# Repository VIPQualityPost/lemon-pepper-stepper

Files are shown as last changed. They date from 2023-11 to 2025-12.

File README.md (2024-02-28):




# Lemon Pepper Stepper Driver
Small, all in one hybrid stepper + BLDC driver, designed to mount to the back of NEMA 14/17 size stepper motors. The board supports up to 48V @ 1.5A with a choice of either step-dir, CAN bus, I2C, UART or USB input. Additionally, there are 5 GPIO broken out that can be used for a second encoder (AB hardware encoder or I2C), endstops or other general purposes. Current sensing is also included on-board.
The boards can easily be assembled by JLC and the design has been cost-optimized, coming in at about $20 per board fully assembled (minus connectors, which need to be modified to sit flat on motor back). 

Due to the high pole pair count of stepper motors, a high resolution (21 bit) magnetic encoder is used, supporting both SPI and hardware ABI position encoding. 
Despite the rather high theoretical performance of this board I think you would need some serious cooling to actually hit the potential 50-70W specs of the parts. A heatsink has been designed and produced that works well with the board, giving a uniform back profile and small fins for heat dissipation.
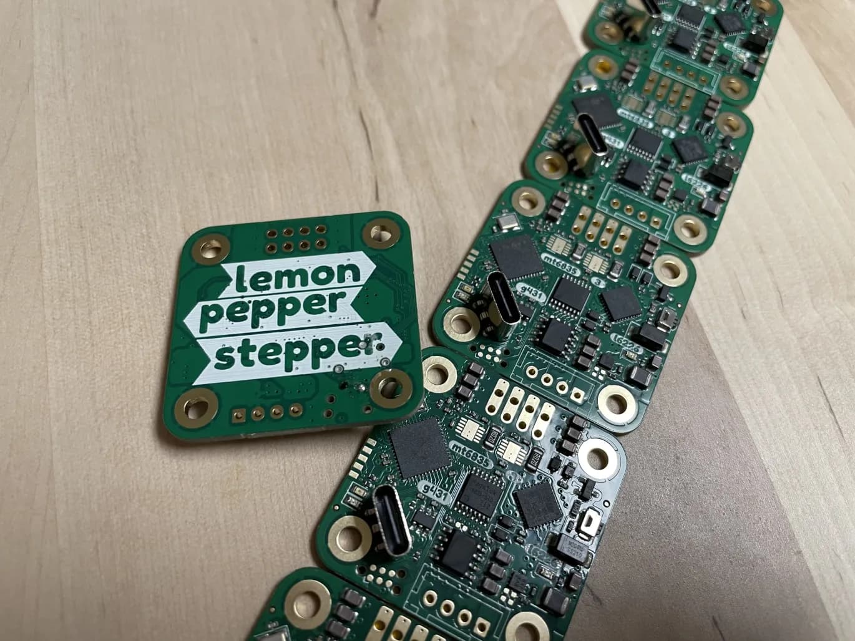
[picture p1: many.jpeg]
Photo of PCB

PCB on motor
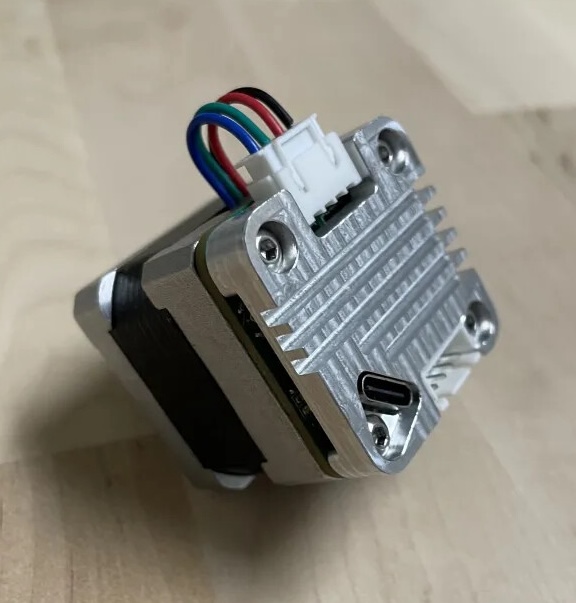
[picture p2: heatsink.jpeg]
Heatsink on motor


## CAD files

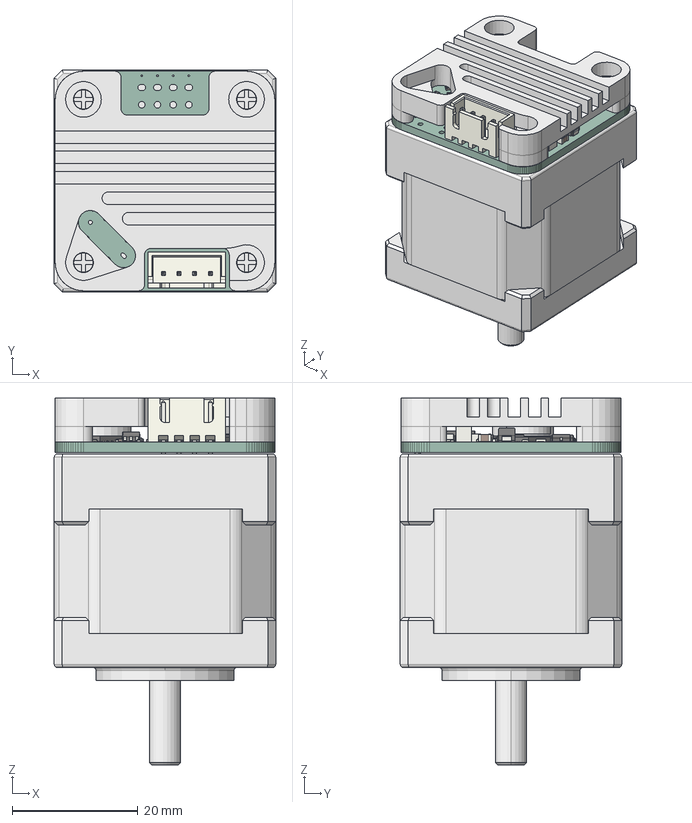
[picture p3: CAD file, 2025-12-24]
mechanical/pcb2blender/lps-assembly.step
35.3 x 35.3 x 58.5 mm
lemon-pepper PCB
6627T38_Stepper Motor

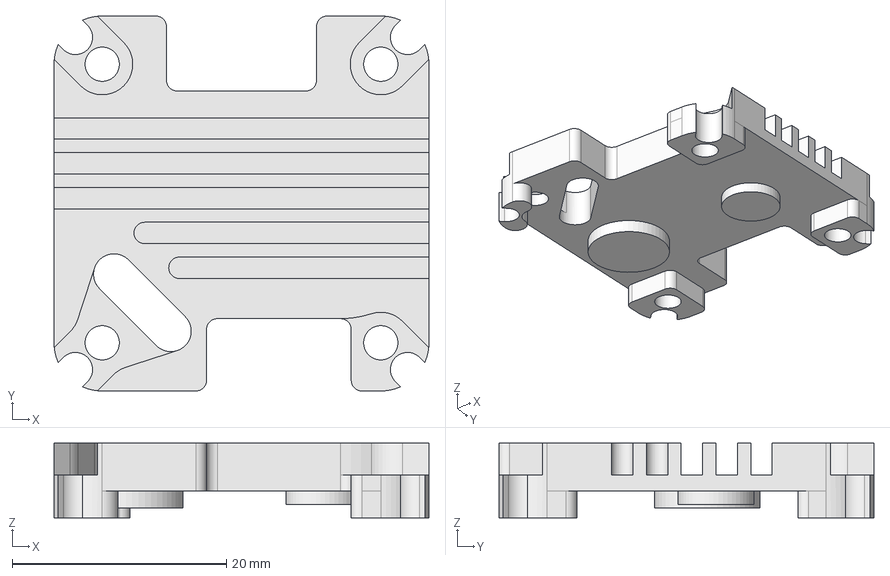
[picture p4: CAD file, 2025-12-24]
mechanical/heatsink-nema-14-17.step
35.0 x 35.0 x 7.00 mm

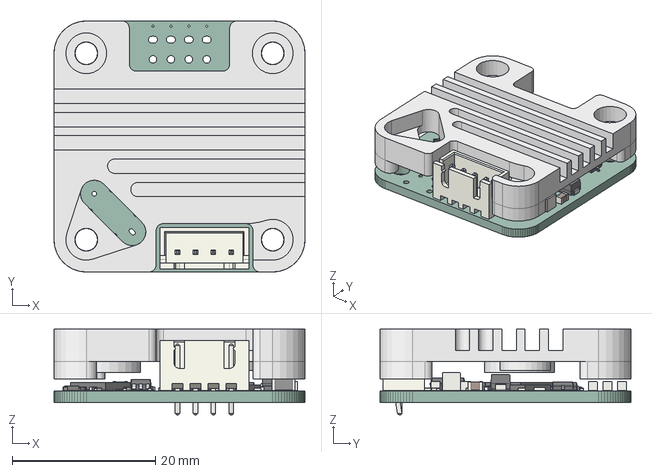
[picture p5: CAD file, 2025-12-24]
mechanical/pcb2blender/lemon-pepper.step
35.0 x 35.0 x 12.0 mm
lemon-pepper PCB

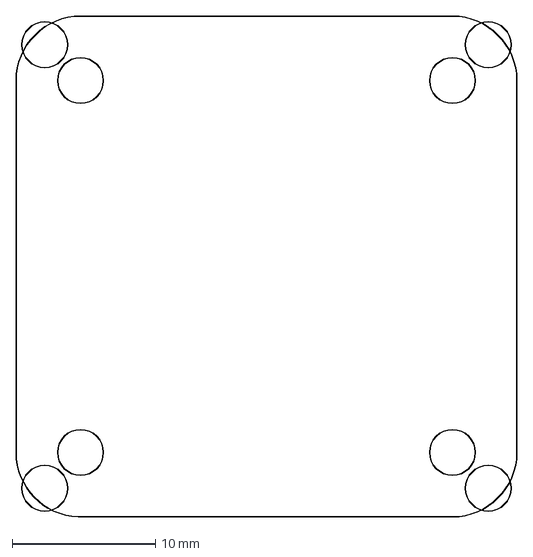
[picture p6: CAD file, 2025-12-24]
mechanical/nema-14-17-hybrid.dxf
35.0 x 35.0 mm

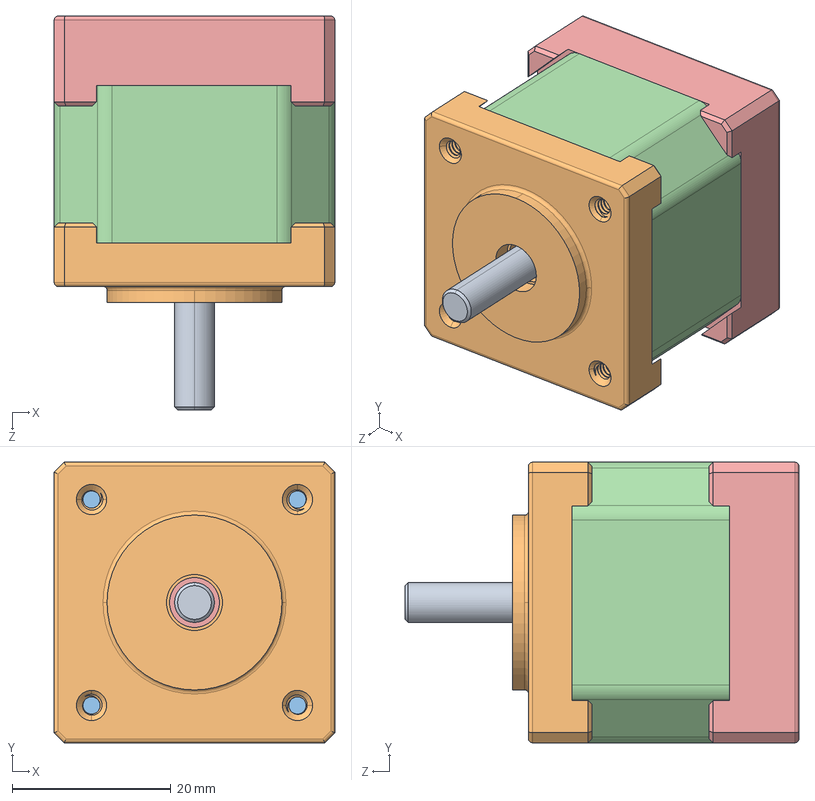
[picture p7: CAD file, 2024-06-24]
mechanical/NEMA_14_motor.step
35.3 x 35.3 x 49.6 mm

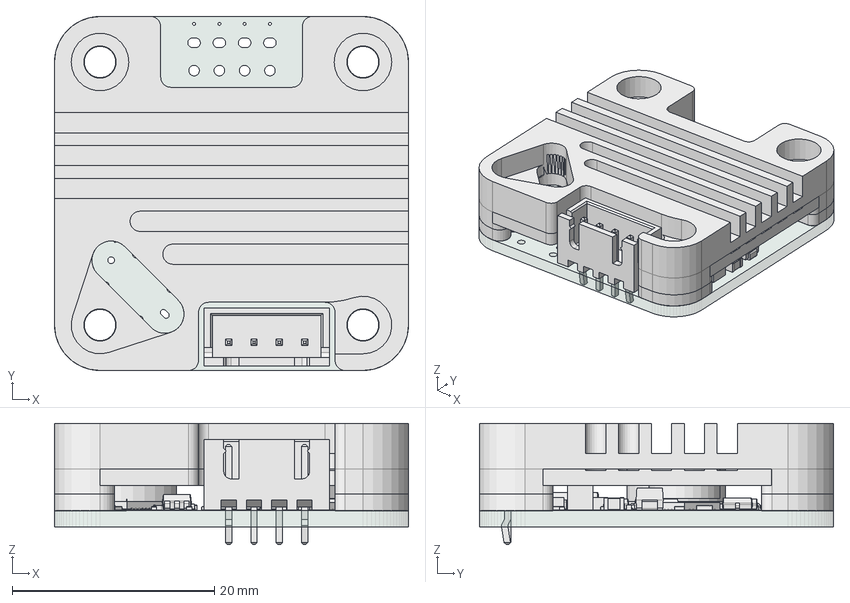
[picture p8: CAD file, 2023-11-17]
mechanical/heatsink.FCStd
35.0 x 35.0 x 12.0 mm
nema-14
lemon-pepper PCB

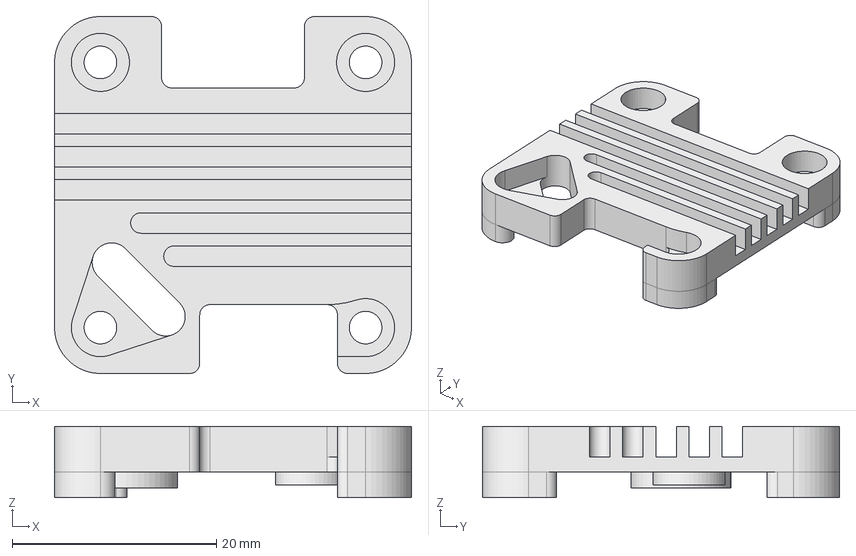
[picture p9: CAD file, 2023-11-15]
mechanical/heatsink-nema-14.step
35.0 x 35.0 x 7.00 mm

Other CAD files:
mechanical/heatsink-nema-14.stl
mechanical/old heatsink/heatsink-nema-14.stl

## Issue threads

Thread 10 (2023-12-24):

Please develop a nema23/34 version

mac7988, 2023-12-24:
There needs to be an affordable integrated controller in the market to be suitable replacement to Clearpath teknic.

I am happy to donate if you can make an open source  bldc verison

VIPQualityPost, 2024-01-22:
Sorry I didn't write back.. I would love to make a larger version, but currently my next plan is for NEMA17.
A similiar project you might find interesting is Funqi Stack which does support NEMA23 I believe, but is a bit more complicated to build: https://community.simplefoc.com/t/the-field-stack-stspin32g4/3032

Closed 2024-01-22.

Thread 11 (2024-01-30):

Current Sensing

egeKeyvan, 2024-01-30:
Hello, thanks for the great design. I was trying to order this board from JLCPCB and unfortunately the MAX49925 current sense module seems to be out of stock.

Do you have any suggestions ?

Is it possible to change the current sensors with a more widely available part ?

VIPQualityPost, 2024-01-31:
Yes, they don't have stock, I requested them to add some to inventory but I don't know when they will come.
If you require it to be assembled, you can arrange with them via Global Sourcing to put the part in your personal inventory (I did this for my boards in the meantime). But actually, if you don't need current sensing, you can leave this part off or place later by hand (it's not too hard if you have a hot air station). The current sensing code is also still in the works.

VIPQualityPost, 2024-01-31:
And to answer the last part: no, there are no other current sensors which fit on this board. Due to the space constraints, it's really impossible to find any other current sensor which supports common mode voltage +48V and fits within the small space. I was previously using hall-effect based current sensors, but the encoder magnet caused interference, so I can't use any of that type.

Closed 2024-02-01.

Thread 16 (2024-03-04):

Feedback on packaging errors of chip MAX49925

fjpaxkm, 2024-03-04:
The number 5 pin of MAX49925 is GND and the number 4 pin is OUT

VIPQualityPost, 2024-03-04:
Thanks, not sure how I missed this!
I had ordered a set of boards with this component laid out but did not test yet. Thank you for the note, I will fix today.

Closed 2024-03-05.

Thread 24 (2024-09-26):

Seperate Gerbers for NEMA14 and 17

Leafy1, 2024-09-26:
Would it be possible to wrap up the Gerber file zips required for each size board its not clear from the releases which size is included.

Copper280z, 2024-09-28:
IIRC the gerbers included in the release are for 14 only. It's easy to double check using the kicad gerber viewer and measure the holes.

The releases are a scripted thing, and I don't think it's easy to script replacing the 14 with 17 edge cuts and hole locations but I've never tried to do it so I'm not positive. In the past 17 sized gerbers were always hand made and added.

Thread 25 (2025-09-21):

Epic: Test Coverage Improvement

3eggert, 2025-09-21:
## Overview
Implement comprehensive test coverage for Lemon Pepper Stepper firmware using virtual hardware testing environments. This epic establishes a robust testing framework using QEMU/Renode emulation and Docker simulation to achieve 80% code coverage without physical hardware, focusing on motor control algorithms, communication protocols, and safety systems.

## Goals
- Achieve 80% line coverage for firmware code
- Establish GoogleTest/GoogleMock testing framework
- Configure QEMU/Renode emulation for ARM testing
- Create Docker-based test environments
- Implement comprehensive test suites for critical components

## Success Criteria
- 80% line coverage overall, 100% for safety-critical code
- Full test suite executes in < 5 minutes
- Zero flaky tests
- Clear test failures with fast feedback loop
- Self-documenting tests with reusable fixtures

## Timeline
Estimated 8-9 weeks with single developer

## Tasks
This epic will be broken down into 10 implementation tasks covering infrastructure setup, test implementation, and documentation.

Closed 2025-09-21.

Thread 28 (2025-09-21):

Create Docker test environment with virtual CAN/Serial interfaces

3eggert, 2025-09-21:
## Parent Epic
#25

## Description
Build Docker container with virtual CAN bus and serial interfaces for system-level testing. This provides an isolated, reproducible environment for integration tests.

## Acceptance Criteria
- [ ] Dockerfile created with necessary tools and dependencies
- [ ] Virtual CAN interface (vcan0) configured and operational
- [ ] Virtual serial ports (socat) for UART testing
- [ ] Container can run QEMU inside for full system simulation
- [ ] docker-compose.yml for easy environment management

## Technical Details
- Base image: Ubuntu 22.04 or Alpine Linux
- Install can-utils for CAN bus tools
- Configure socat for virtual serial ports
- Set up SocketCAN for CAN communication
- Mount firmware directory as volume
- Create test harness scripts inside container

## Dependencies
- Docker 20+ installed
- Understanding of Docker networking
- Linux kernel with CAN support

Closed 2025-09-21.

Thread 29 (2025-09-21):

Implement HAL mock layer using GoogleMock

3eggert, 2025-09-21:
## Parent Epic
#25

## Description
Create mock implementations of the Hardware Abstraction Layer using GoogleMock. This enables unit testing of business logic without hardware dependencies.

## Acceptance Criteria
- [ ] Mock classes created for all HAL interfaces
- [ ] GPIO, ADC, PWM, UART, CAN mocks implemented
- [ ] Timer and interrupt mocks with controllable behavior
- [ ] Mock expectations can be set and verified
- [ ] Example tests demonstrate mock usage

## Technical Details
- Create mock_hal.h with GoogleMock classes
- Implement MOCK_METHOD for each HAL function
- Support both strict and nice mock modes
- Create helper functions for common mock setups
- Ensure thread-safety for multi-threaded tests

## Dependencies
- Task 001 (GoogleTest/Mock setup) completed
- Understanding of existing HAL interface
- GoogleMock documentation

Closed 2025-09-21.

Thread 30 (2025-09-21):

Write FOC algorithm unit tests

3eggert, 2025-09-21:
## Parent Epic
#25

## Description
Implement comprehensive unit tests for Field-Oriented Control algorithms including Park/Clarke transforms, Space Vector Modulation, and control loops.

## Acceptance Criteria
- [ ] Park transform tests with known input/output values
- [ ] Clarke transform tests with mathematical validation
- [ ] SVM (Space Vector Modulation) tests for all sectors
- [ ] PID controller tests with various setpoints
- [ ] Current/velocity/position control loop tests
- [ ] Edge cases and boundary conditions covered

## Technical Details
- Test mathematical correctness against reference implementations
- Use floating-point comparison with appropriate epsilon
- Test both forward and inverse transforms
- Validate steady-state and transient responses
- Test saturation and anti-windup mechanisms
- Include performance regression tests

## Dependencies
- Task 001 (GoogleTest setup) completed
- Task 004 (HAL mocks) for hardware interfaces
- FOC algorithm documentation
- Reference test vectors

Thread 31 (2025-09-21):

Status?

3eggert, 2025-09-21:
Hi I would like to use and continue development on [lemon-pepper-stepper](https://github.com/VIPQualityPost/lemon-pepper-stepper).
For me the current status of it is unclear, could you give a short list of whats known to work and what not?
Also some kind of license would be nice.
Happy hacking

Thorsten

PS:
Sorry for the issues I entered.

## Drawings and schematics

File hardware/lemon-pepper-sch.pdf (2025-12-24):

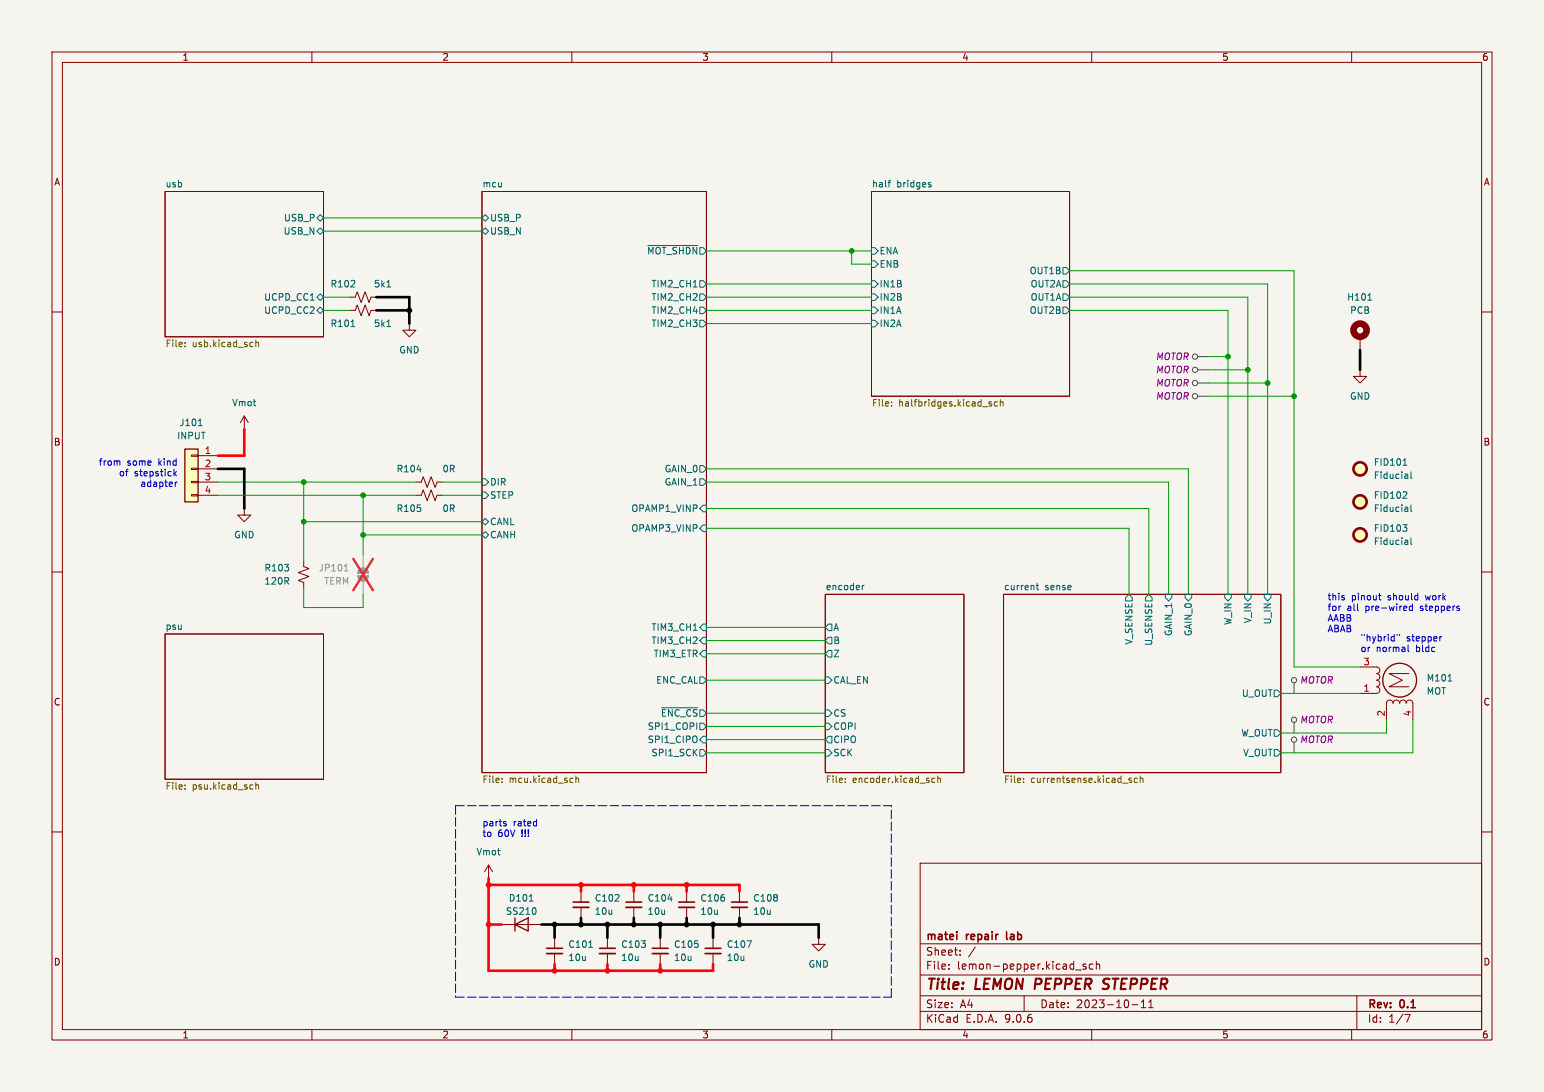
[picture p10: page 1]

half bridges File: halfbridges.kicad_sch B
current sense File: currentsense.kicad_sch OUT2B OUT1A OUT2A OUT1B

this pinout should work

File: lemon-pepper.kicad_sch Sheet: / matei repair lab

Id: 1/7 Title: LEMON PEPPER STEPPER

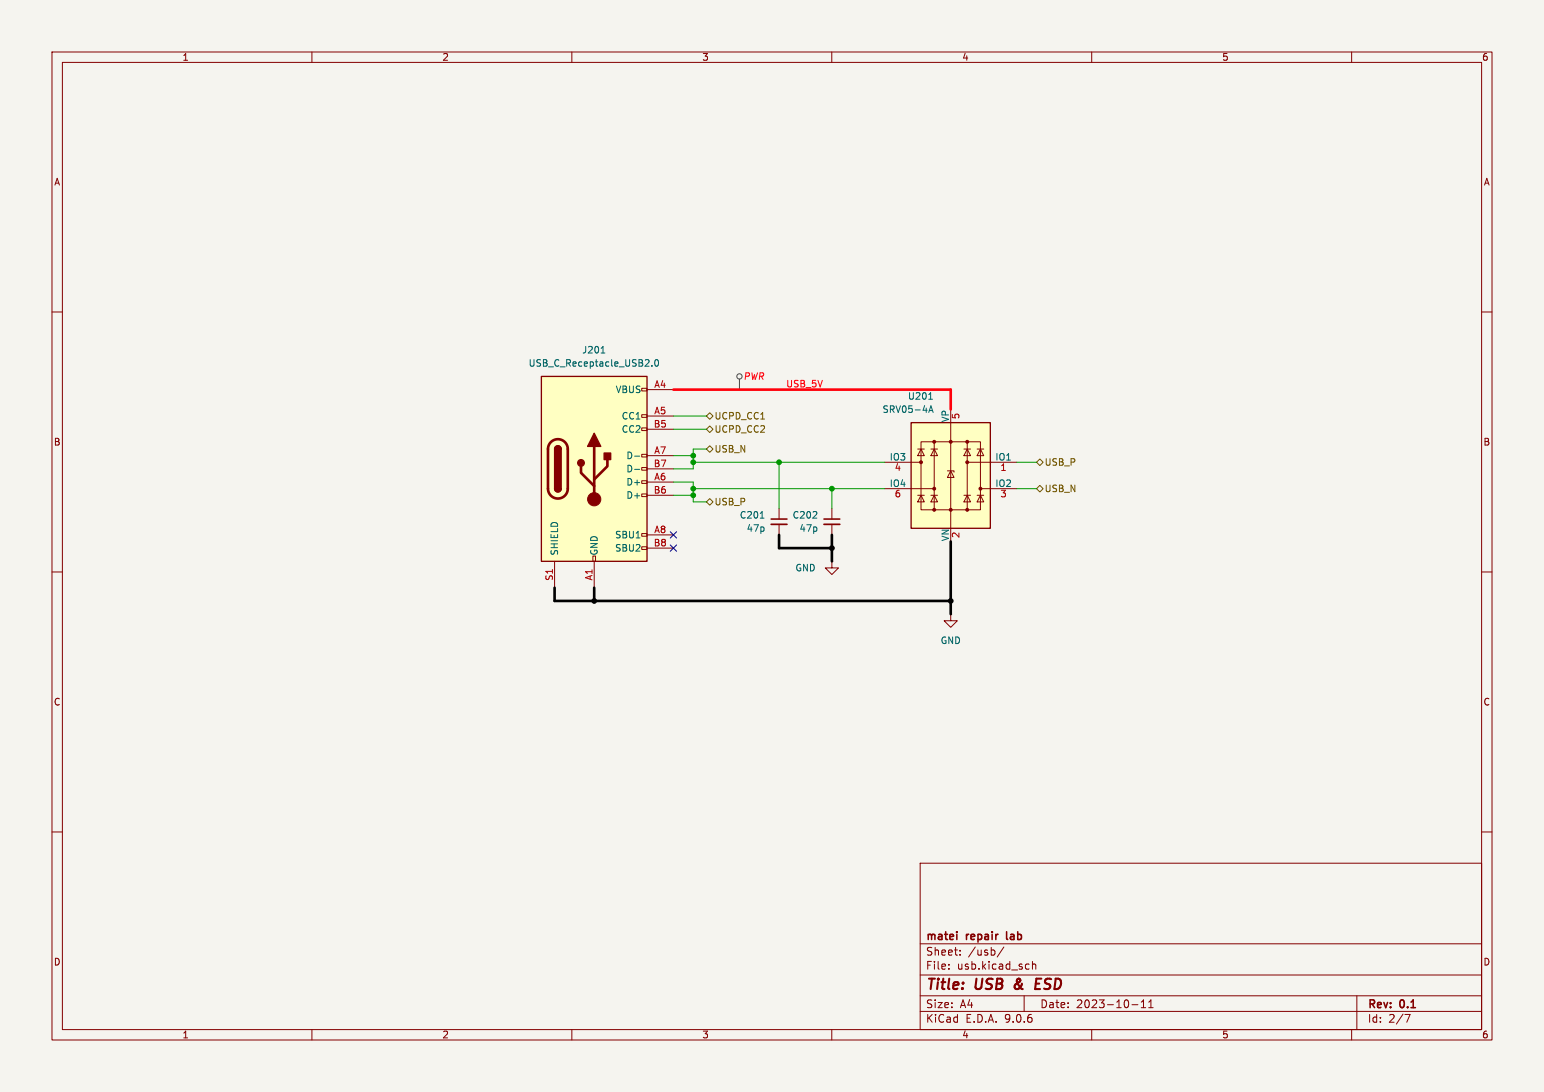
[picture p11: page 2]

File: usb.kicad_sch Sheet: /usb/ matei repair lab C201
47p GND

Id: 2/7 Title: USB & ESD

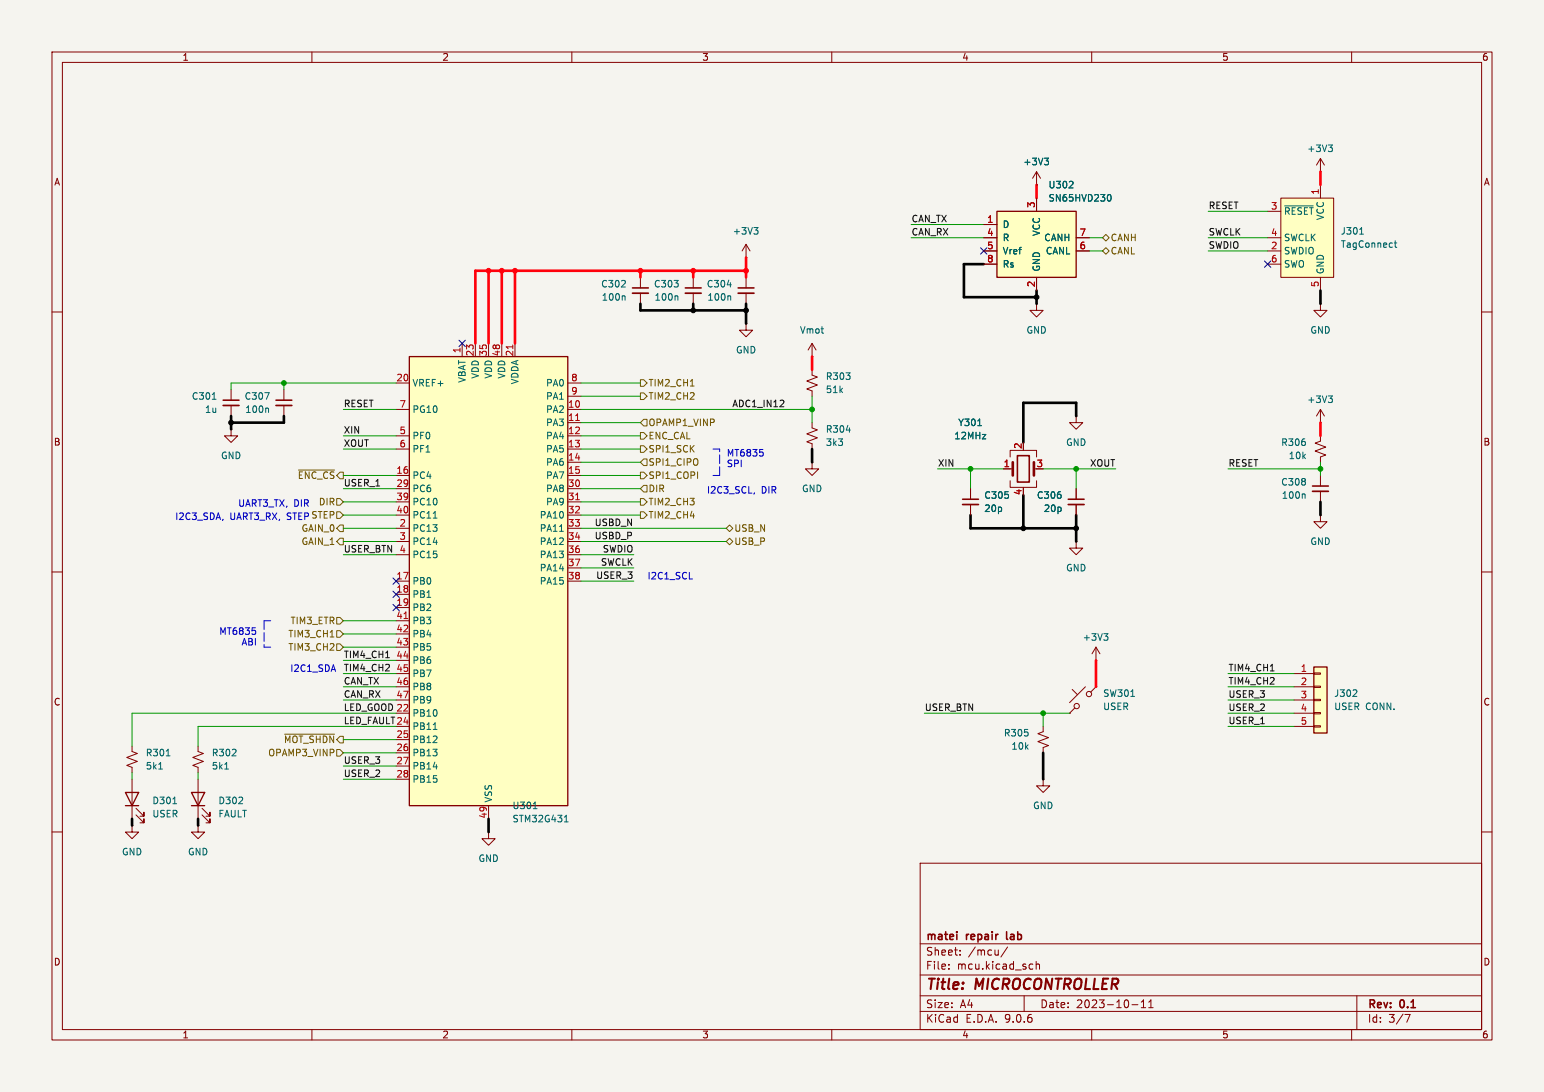
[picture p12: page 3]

5 ~{RESET} 3 SWCLK 4 SWDIO 2 SWO 6

1 VDD 23 VDD 35 VSS 49 VDD 48 VDDA 21 PA0 8 PA1 9 PA2 10 PA3 11 PA4 12 PA5 13 PA6 14 PA7 15 PA8 30 PA9 31 PA10 32 PA11 33 PA12 34 PA13 36 PA14 37 PA15 38 U301 STM32G431 C307

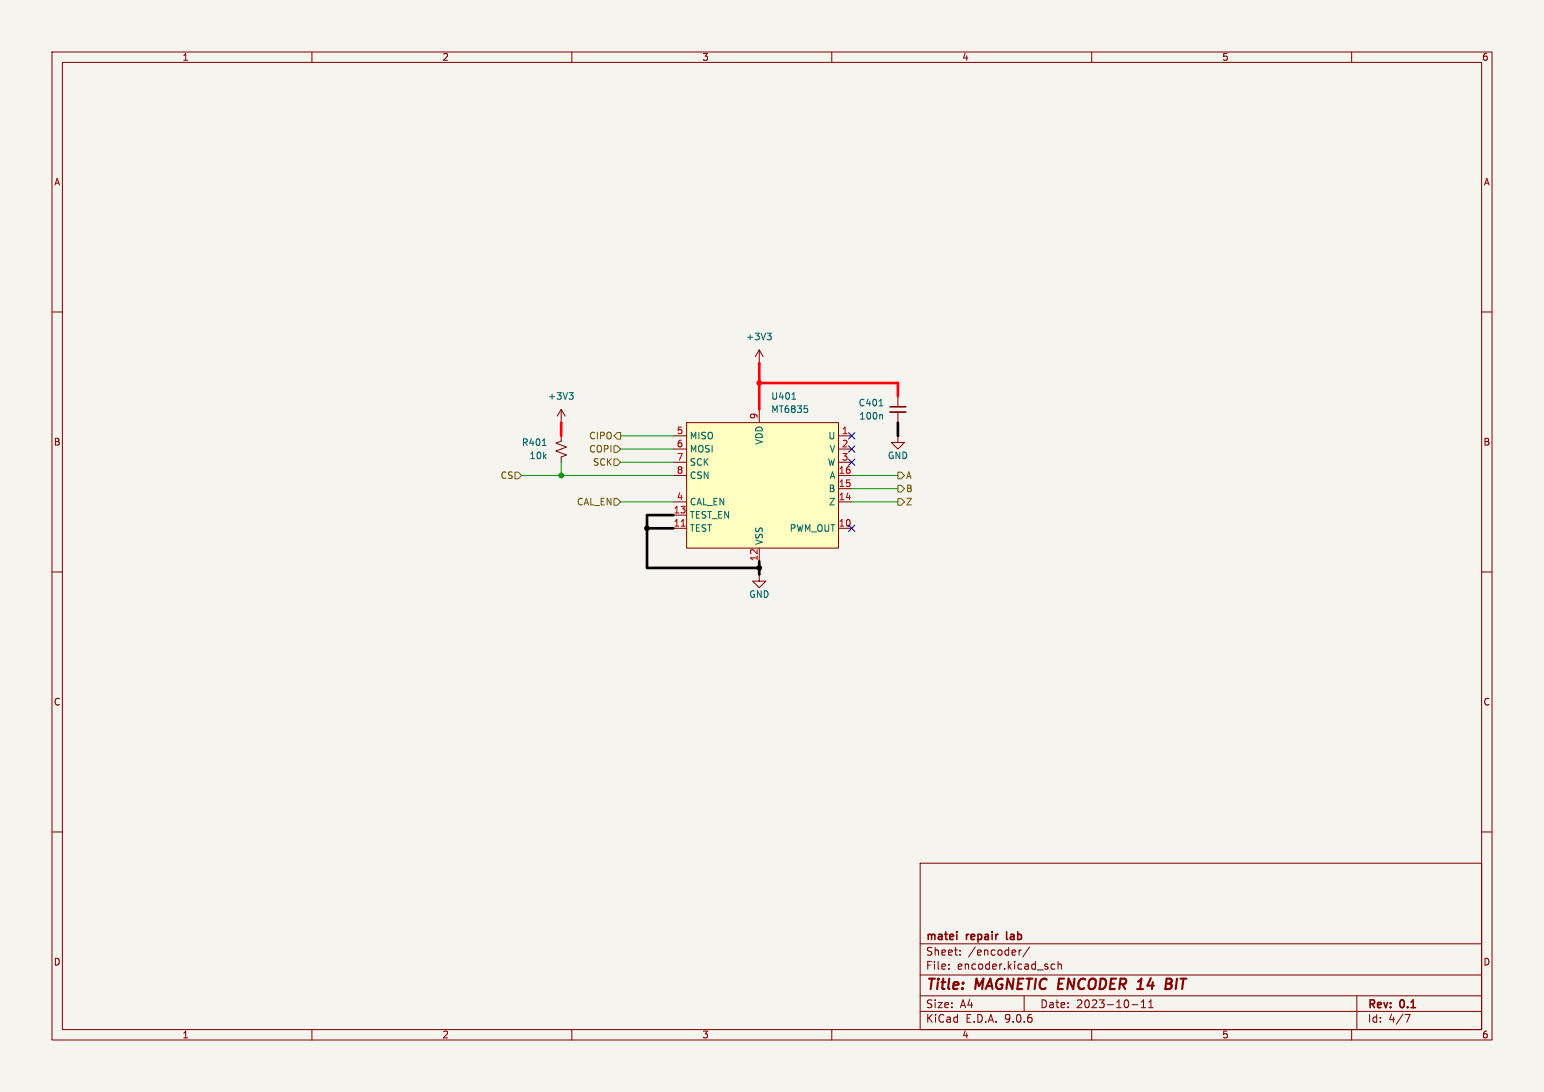
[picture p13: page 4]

9 VSS 12 U401 MT6835 GND COPI CS A

File: encoder.kicad_sch Sheet: /encoder/ matei repair lab

Id: 4/7 Title: MAGNETIC ENCODER 14 BIT

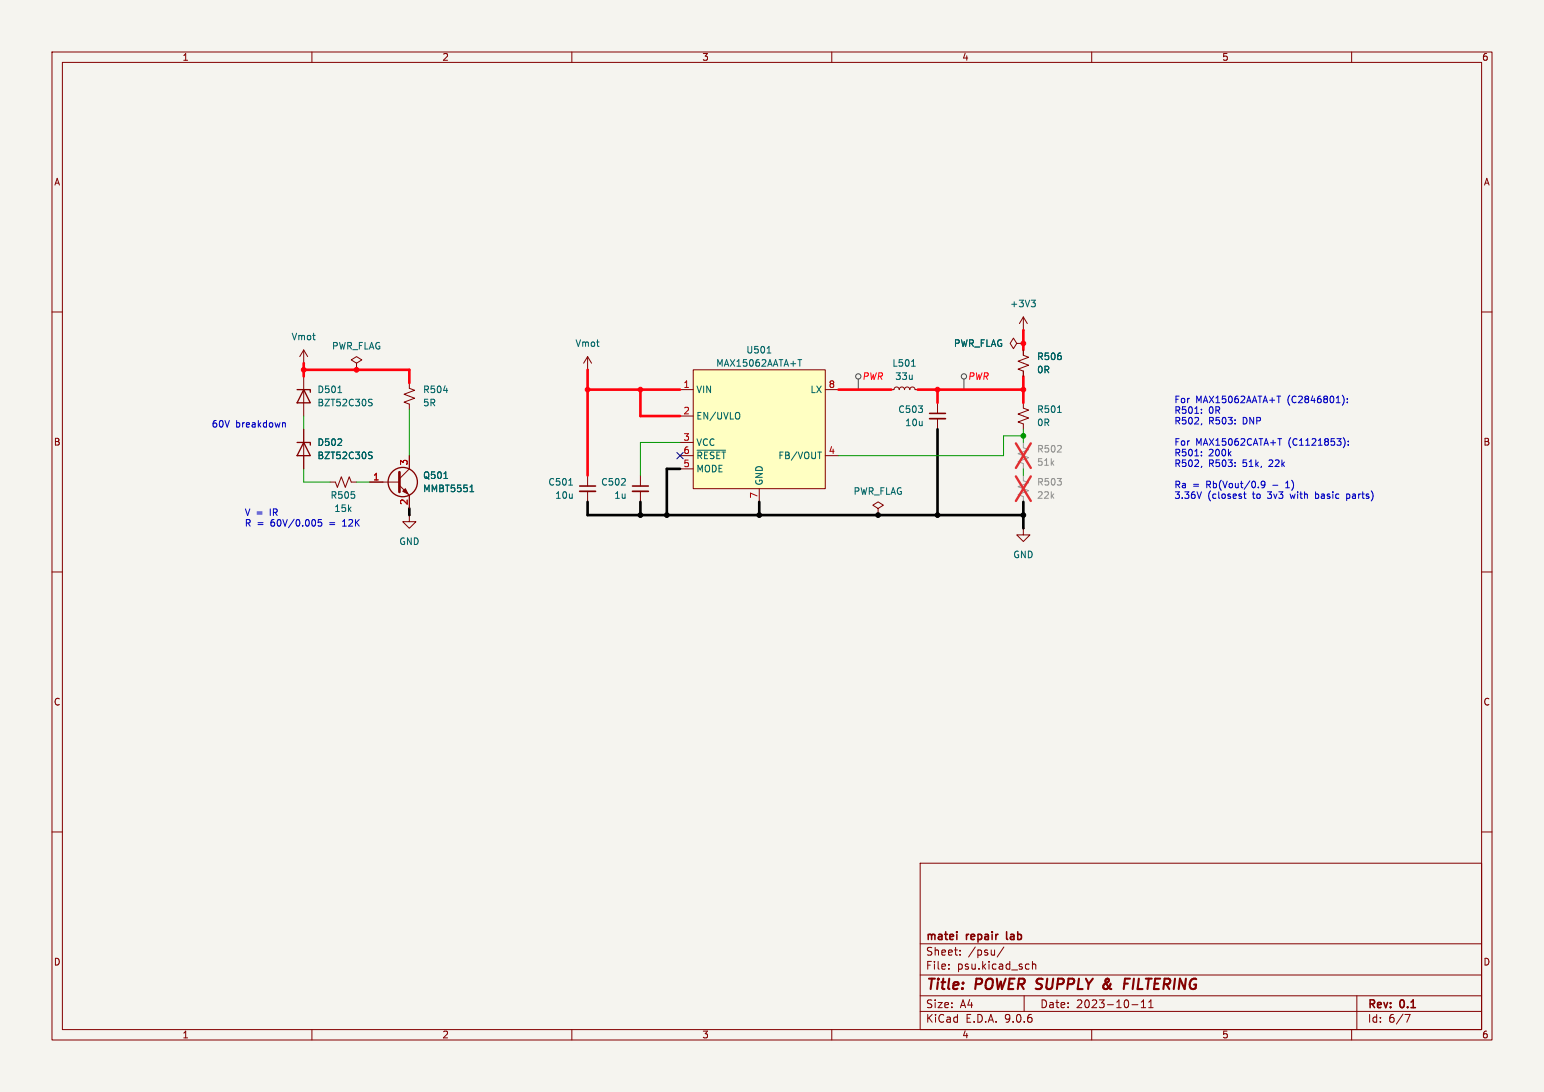
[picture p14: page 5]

File: psu.kicad_sch Sheet: /psu/ matei repair lab

Id: 6/7 Title: POWER SUPPLY & FILTERING

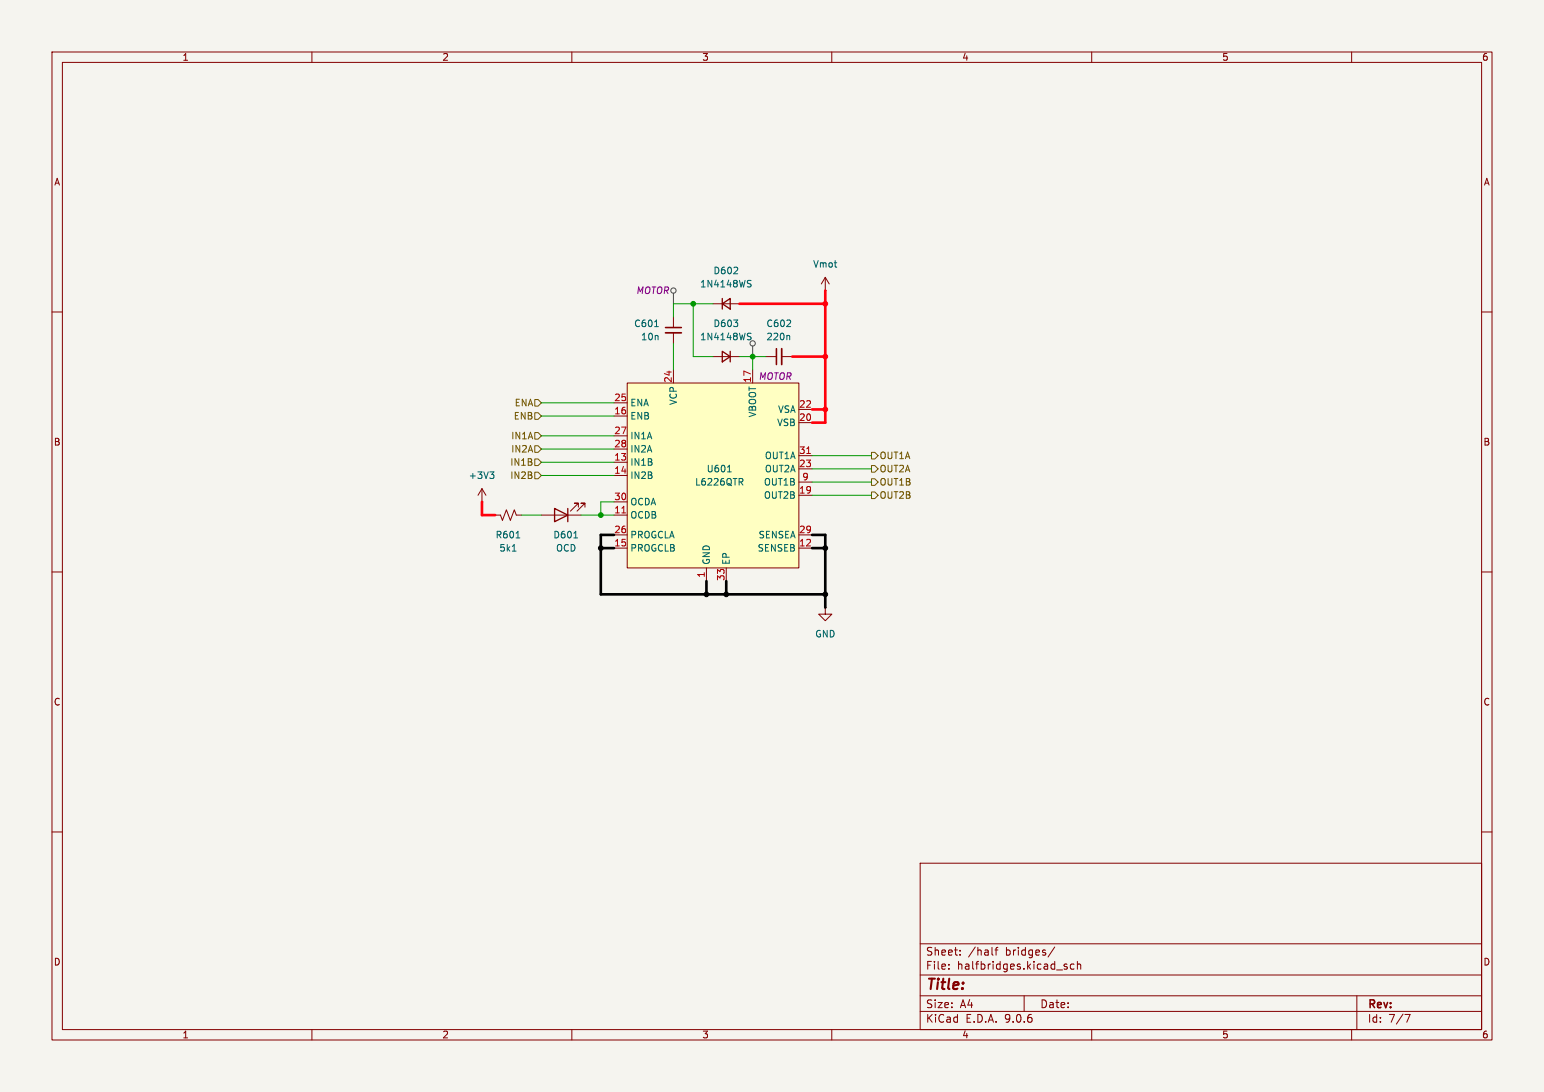
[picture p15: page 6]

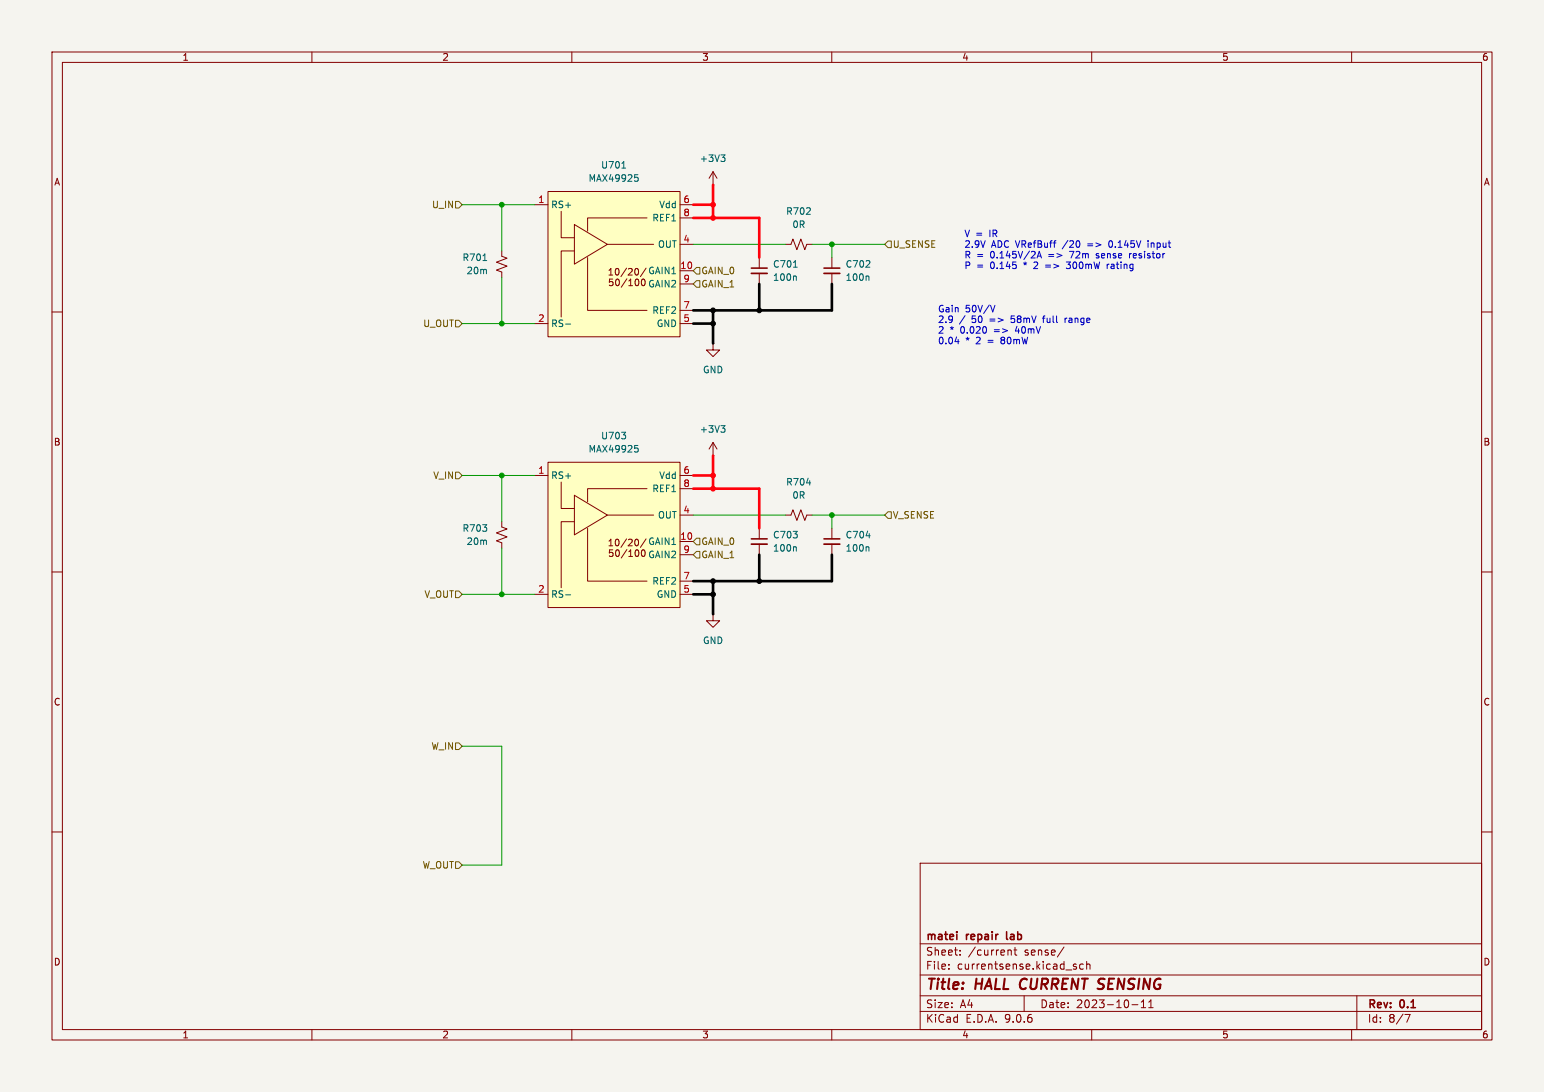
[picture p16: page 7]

Id: 8/7 Title: HALL CURRENT SENSING

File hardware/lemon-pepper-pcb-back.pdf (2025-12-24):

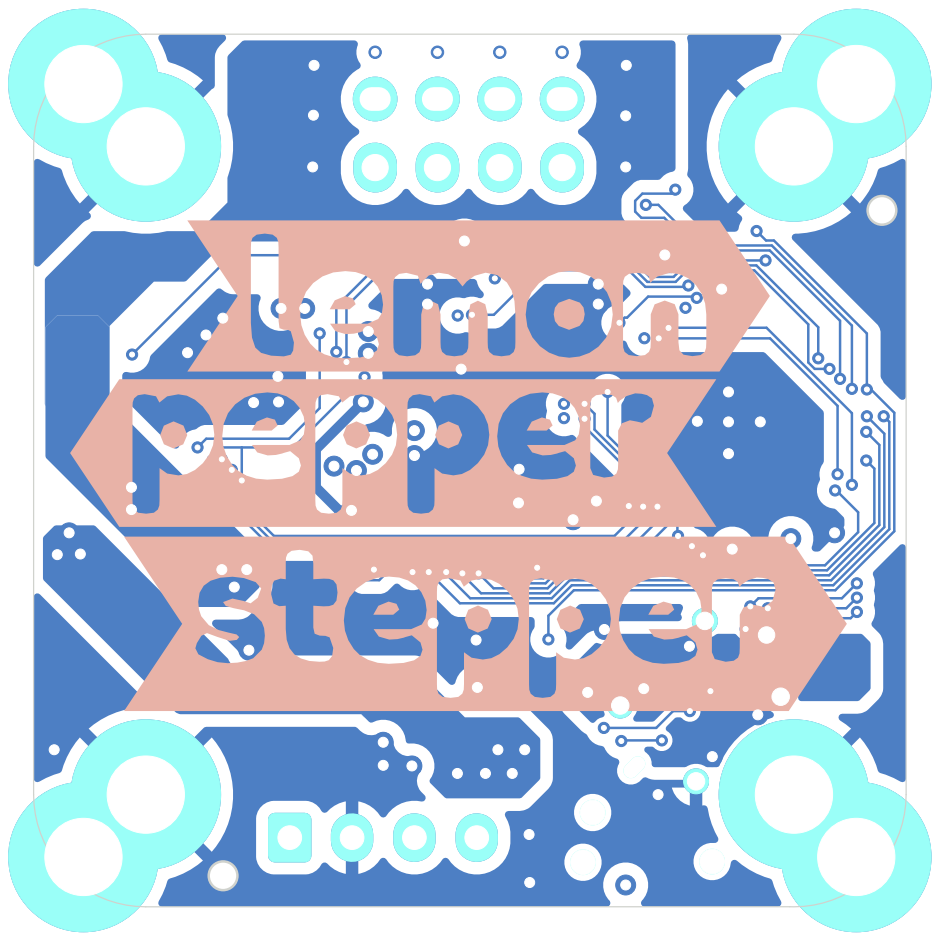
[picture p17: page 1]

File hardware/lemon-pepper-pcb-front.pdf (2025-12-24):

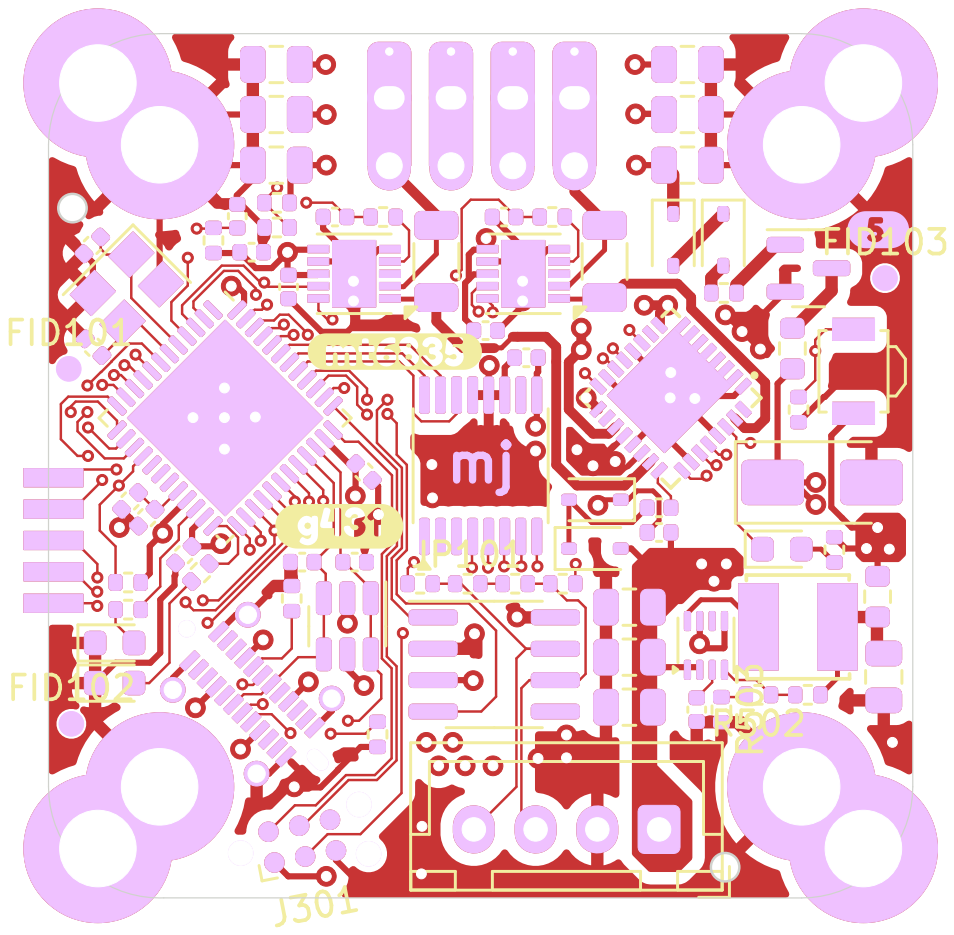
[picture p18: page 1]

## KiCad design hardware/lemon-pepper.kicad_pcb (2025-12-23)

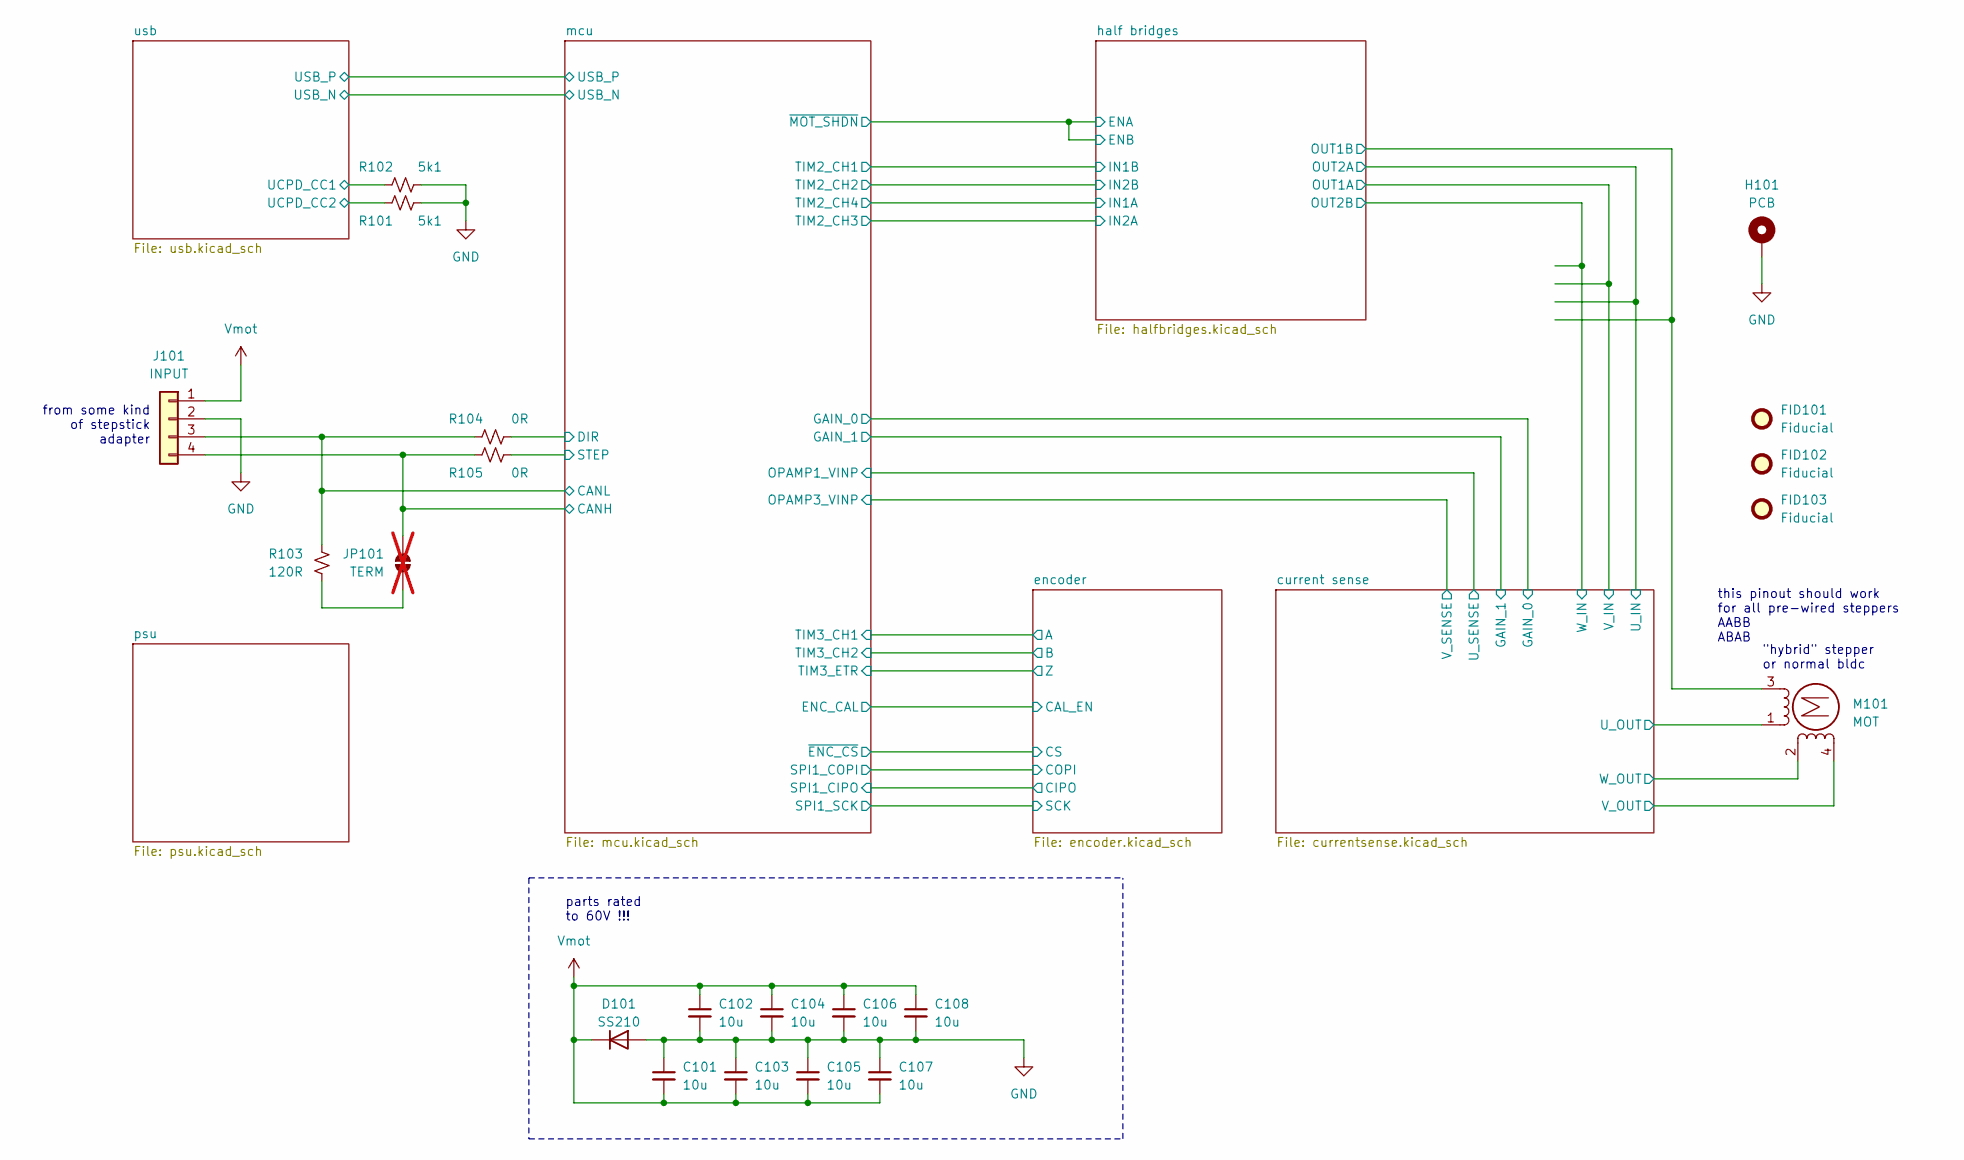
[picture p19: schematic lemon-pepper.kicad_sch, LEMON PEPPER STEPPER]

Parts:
C101, C102, C103, C104, C105, C106, C107, C108: 10u; C_0805_2012Metric; LCSC ID C440198
D101: SS210; D_SMA; LCSC ID C14996
FID101, FID102, FID103: Fiducial; Fiducial_0.5mm_Mask1mm
H101: PCB; nema-14-17-hybrid
J101: INPUT; JST_XH_B4B-XH-A_1x04_P2.50mm_Vertical
JP101: TERM; R_0402_1005Metric; not fitted
M101: MOT; XH2.54 4P
R101, R102: 5k1; R_0402_1005Metric; LCSC ID C25905
R103: 120R; R_0402_1005Metric; LCSC ID C25079
R104, R105: 0R; R_0402_1005Metric; LCSC ID C17168

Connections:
/current sense/U_OUT: M101.1; also elsewhere on the board
/current sense/V_OUT: M101.4; also elsewhere on the board
/current sense/W_IN: M101.2 (-); also elsewhere on the board
/half bridges/OUT1B: M101.3; also elsewhere on the board
/mcu/CANH: J101.4, JP101.1 (A), R105.2; also elsewhere on the board
/mcu/CANL: J101.3, R103.1, R104.1; also elsewhere on the board
/mcu/DIR: R104.2; also elsewhere on the board
/mcu/STEP: R105.1; also elsewhere on the board
/usb/UCPD_CC1: R102.1; also elsewhere on the board
/usb/UCPD_CC2: R101.2; also elsewhere on the board
GND: C101.1, C102.2, C103.1, C104.2, C105.1, C106.2, C107.1, C108.2, D101.2 (A), H101.1, J101.2, R101.1, R102.2; also elsewhere on the board
unnamed: JP101.2 (B), R103.2
Vmot: C101.2, C102.1, C103.2, C104.1, C105.2, C106.1, C107.2, C108.1, D101.1 (K), J101.1; also elsewhere on the board

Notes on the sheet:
this pinout should work for all pre-wired steppers AABB ABAB
parts rated to 60V !!!
from some kind of stepstick adapter
"hybrid" stepper or normal bldc

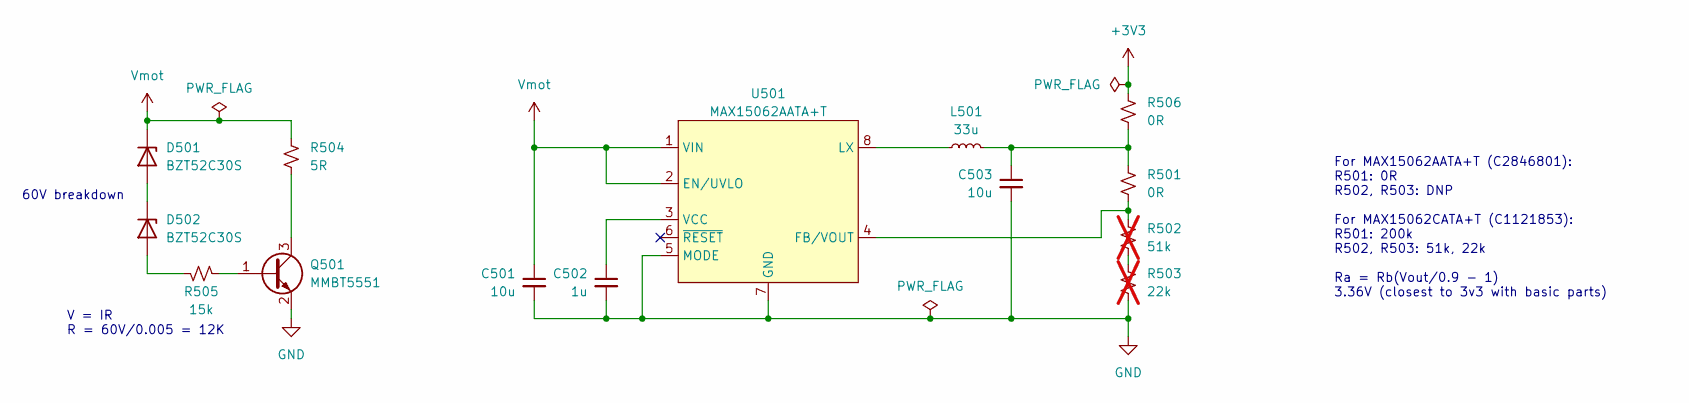
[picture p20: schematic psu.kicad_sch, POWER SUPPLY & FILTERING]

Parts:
C501, C503: 10u; C_0805_2012Metric; LCSC ID C440198
C502: 1u; C_0402_1005Metric; LCSC ID C52923
D501, D502: BZT52C30S; D_SOD-323; LCSC ID C19077418
L501: 33u; IND-SMD_L4.0-W4.0; LCSC ID C602034
Q501: MMBT5551; SOT-23; LCSC ID C2145
R501: 0R; R_0402_1005Metric; LCSC ID C17168
R502: 51k; R_0402_1005Metric; LCSC ID C25794; not fitted
R503: 22k; R_0402_1005Metric; LCSC ID C25768; not fitted
R504: 5R; R_0603_1608Metric; LCSC ID C22936
R505: 15k; R_0402_1005Metric; LCSC ID C25756
R506: 0R; R_0603_1608Metric; LCSC ID C21189
U501: MAX15062AATA+T; TDFN-8-1EP_2x2mm_P0.5mm_EP0.8x1.2mm; LCSC ID C2846801

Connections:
+3V3: R506.1; also elsewhere on the board
GND: C501.2, C502.2, C503.2, Q501.2 (E), R503.2, U501.5 (MODE), U501.7 (GND); also elsewhere on the board
unnamed: C503.1, L501.2, R501.1, R506.2
unnamed: D501.2 (A), D502.1 (K)
unnamed: D502.2 (A), R505.1
unnamed: Q501.1 (B), R505.2
unnamed: Q501.3 (C), R504.2
unnamed: R502.2, R503.1
unnamed: R501.2, R502.1, U501.4 (FB/VOUT)
unnamed: L501.1, U501.8 (LX)
unnamed: C502.1, U501.3 (VCC)
Vmot: C501.1, D501.1 (K), R504.1, U501.1 (VIN), U501.2 (EN/UVLO); also elsewhere on the board

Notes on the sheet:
60V breakdown
For MAX15062AATA+T (C2846801): R501: 0R R502, R503: DNP For MAX15062CATA+T (C1121853): R501: 200k R502, R503: 51k, 22k Ra = Rb(Vout/0.9 - 1) 3.36V (closest to 3v3 with basic parts)
V = IR R = 60V/0.005 = 12K

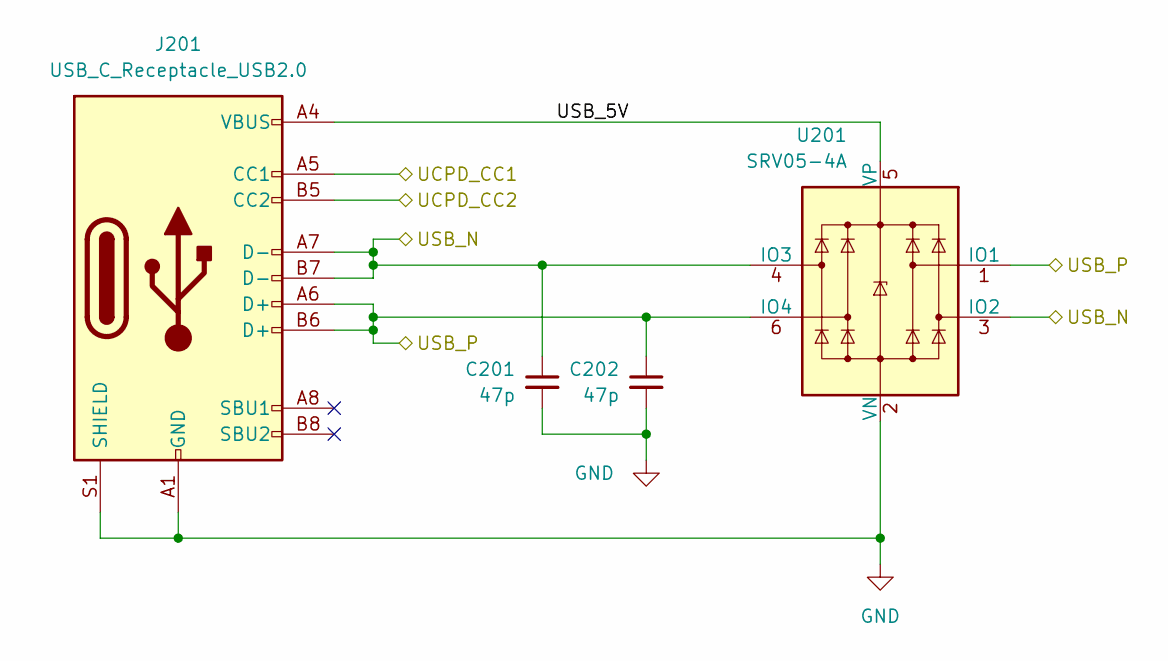
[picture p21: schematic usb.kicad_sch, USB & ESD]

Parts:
C201, C202: 47p; C_0402_1005Metric; LCSC ID C1567
J201: USB_C_Receptacle_USB2.0; usb_c; LCSC ID C963223
U201: SRV05-4A; SOT-23-6; LCSC ID C20615829

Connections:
/mcu/USBD_N: C201.1, J201.A7 (D-), J201.B7 (D-), U201.3 (IO2), U201.4 (IO3); also elsewhere on the board
/mcu/USBD_P: C202.1, J201.A6 (D+), J201.B6 (D+), U201.1 (IO1), U201.6 (IO4); also elsewhere on the board
/usb/UCPD_CC1: J201.A5 (CC1); also elsewhere on the board
/usb/UCPD_CC2: J201.B5 (CC2); also elsewhere on the board
/usb/USB_5V: J201.A4 (VBUS), J201.A9 (VBUS), J201.B4 (VBUS), J201.B9 (VBUS), U201.5 (VP)
GND: C201.2, C202.2, J201.A1 (GND), J201.A12 (GND), J201.B1 (GND), J201.B12 (GND), J201.S1 (SHIELD), U201.2 (VN); also elsewhere on the board

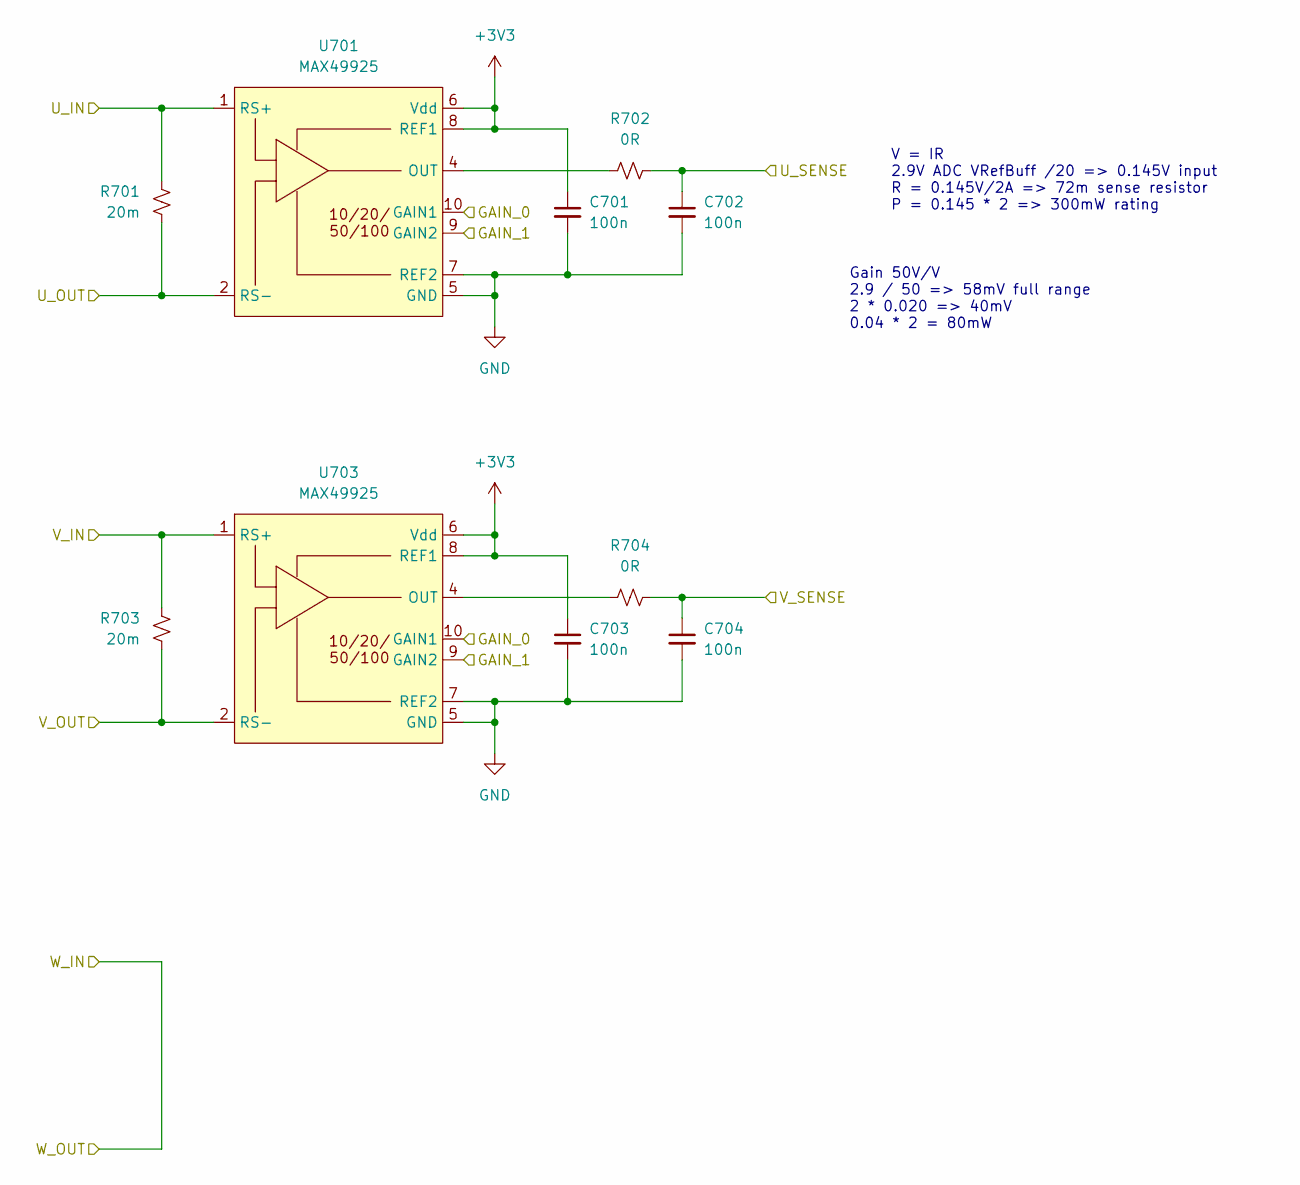
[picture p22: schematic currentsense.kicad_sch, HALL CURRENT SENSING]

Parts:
C701, C702, C703, C704: 100n; C_0402_1005Metric; LCSC ID C307331
R701, R703: 20m; R_1206_3216Metric; LCSC ID C393094
R702, R704: 0R; R_0402_1005Metric; LCSC ID C17168
U701, U703: MAX49925; DFN-10-1EP_3x3mm_P0.5mm_EP1.75x2.7mm; LCSC ID C19193612

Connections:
+3V3: C701.1, C703.1, U701.6 (Vdd), U701.8 (REF1), U703.6 (Vdd), U703.8 (REF1); also elsewhere on the board
/current sense/GAIN_0: U701.10 (GAIN1), U703.10 (GAIN1); also elsewhere on the board
/current sense/GAIN_1: U701.9 (GAIN2), U703.9 (GAIN2); also elsewhere on the board
/current sense/U_IN: R701.1, U701.1 (RS+); also elsewhere on the board
/current sense/U_OUT: R701.2, U701.2 (RS-); also elsewhere on the board
/current sense/U_SENSE: C702.1, R702.2; also elsewhere on the board
/current sense/V_IN: R703.1, U703.1 (RS+); also elsewhere on the board
/current sense/V_OUT: R703.2, U703.2 (RS-); also elsewhere on the board
/current sense/V_SENSE: C704.1, R704.2; also elsewhere on the board
GND: C701.2, C702.2, C703.2, C704.2, U701.5 (GND), U701.7 (REF2), U701.11 (EP), U703.5 (GND), U703.7 (REF2), U703.11 (EP); also elsewhere on the board
unnamed: R702.1, U701.4 (OUT)
unnamed: R704.1, U703.4 (OUT)

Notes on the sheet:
Gain 50V/V 2.9 / 50 => 58mV full range 2 * 0.020 => 40mV 0.04 * 2 = 80mW
V = IR 2.9V ADC VRefBuff /20 => 0.145V input R = 0.145V/2A => 72m sense resistor P = 0.145 * 2 => 300mW rating

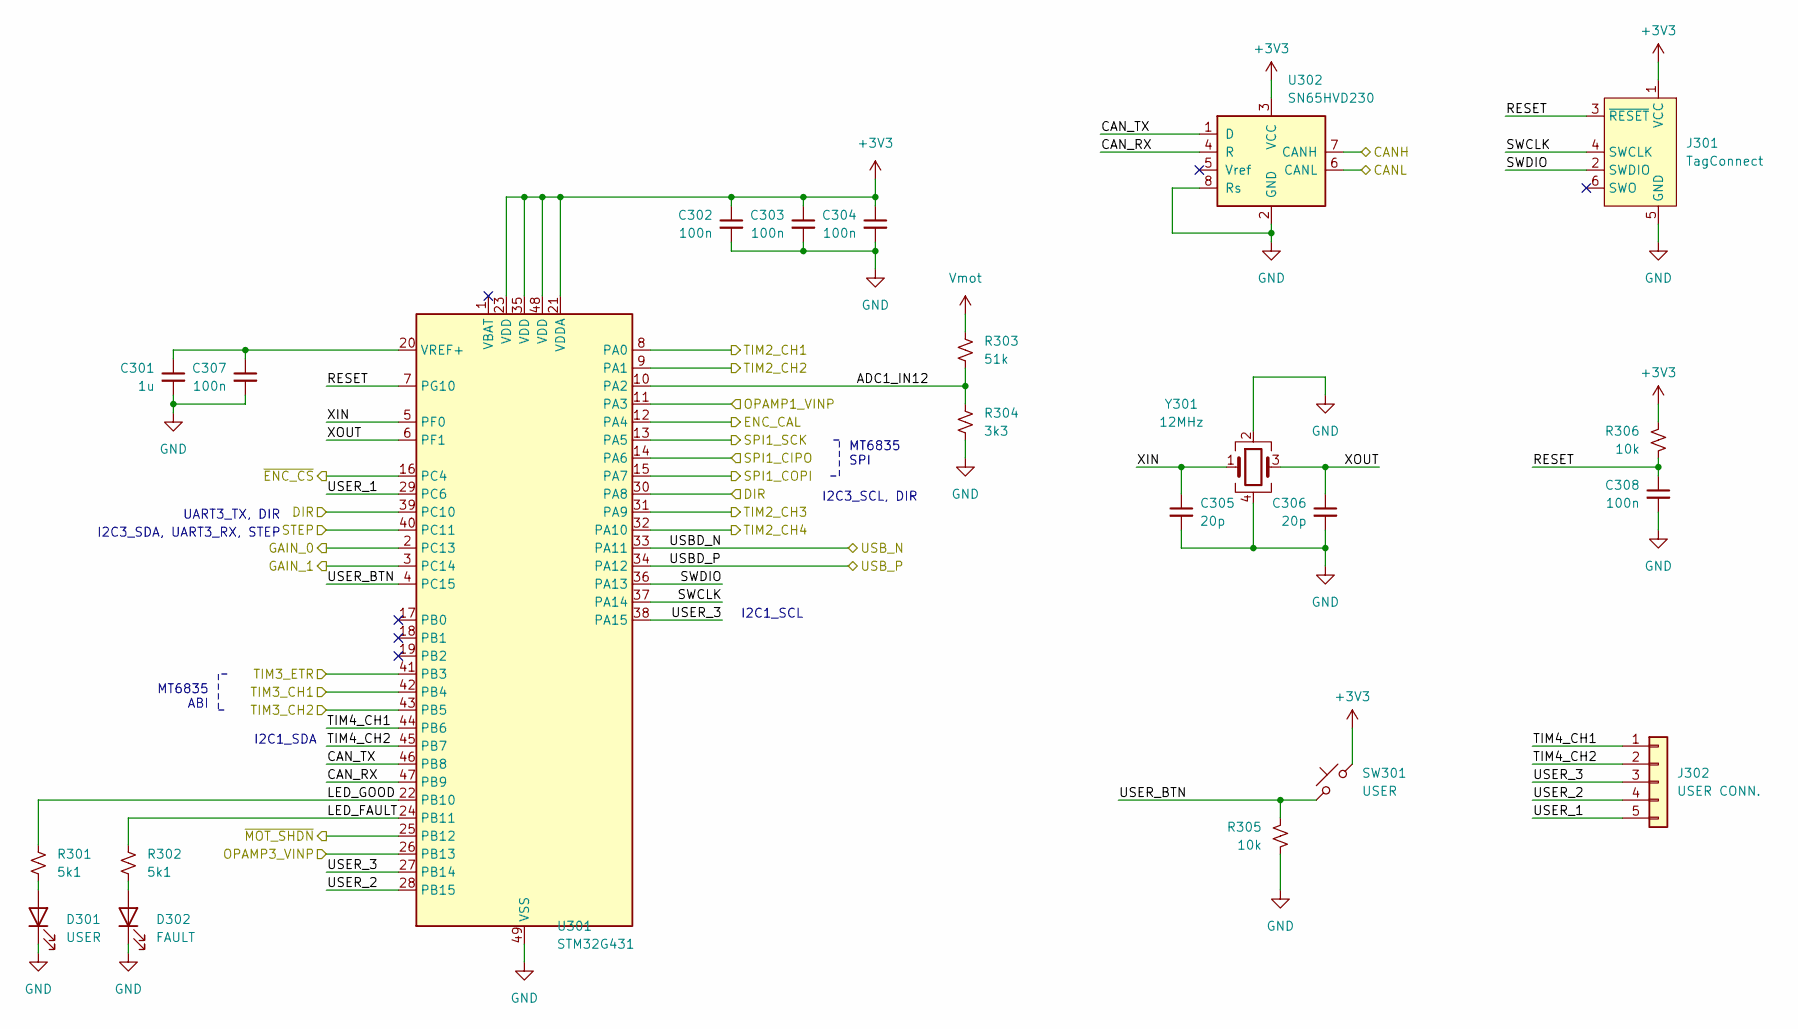
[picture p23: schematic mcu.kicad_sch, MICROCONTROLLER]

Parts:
C301: 1u; C_0402_1005Metric; LCSC ID C52923
C302, C303, C304, C307, C308: 100n; C_0402_1005Metric; LCSC ID C307331
C305, C306: 20p; C_0402_1005Metric; LCSC ID C1554
D301: USER; D_0603_1608Metric; LCSC ID C2290
D302: FAULT; D_0603_1608Metric; LCSC ID C2286
J301: TagConnect; Tag-Connect_TC2030-IDC-NL_2x03_P1.27mm_Vertical
J302: USER CONN.; PinHeader_1x05_P1.27mm_SMD
R301, R302: 5k1; R_0402_1005Metric; LCSC ID C25905
R303: 51k; R_0402_1005Metric; LCSC ID C25794
R304: 3k3; R_0402_1005Metric; LCSC ID C25890
R305, R306: 10k; R_0402_1005Metric; LCSC ID C25744
SW301: USER; SW_SPST_B3U-3000P; LCSC ID C963349
U301: STM32G431; QFN-48-1EP_7x7mm_P0.5mm_EP5.6x5.6mm; LCSC ID C529356
U302: SN65HVD230; SOIC-8_3.9x4.9mm_P1.27mm; LCSC ID C12084
Y301: 12MHz; Crystal_SMD_3225-4Pin_3.2x2.5mm; LCSC ID C9002

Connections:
+3V3: C302.1, C303.1, C304.1, J301.1 (VCC), R306.1, SW301.2, U301.21 (VDDA), U301.23 (VDD), U301.35 (VDD), U301.48 (VDD), U302.3 (VCC); also elsewhere on the board
/current sense/GAIN_0: U301.2 (PC13); also elsewhere on the board
/current sense/GAIN_1: U301.3 (PC14); also elsewhere on the board
/current sense/U_SENSE: U301.11 (PA3); also elsewhere on the board
/current sense/V_SENSE: U301.26 (PB13); also elsewhere on the board
/encoder/A: U301.42 (PB4); also elsewhere on the board
/encoder/B: U301.43 (PB5); also elsewhere on the board
/encoder/CAL_EN: U301.12 (PA4); also elsewhere on the board
/encoder/CIPO: U301.14 (PA6); also elsewhere on the board
/encoder/COPI: U301.15 (PA7); also elsewhere on the board
/encoder/CS: U301.16 (PC4); also elsewhere on the board
/encoder/SCK: U301.13 (PA5); also elsewhere on the board
/encoder/Z: U301.41 (PB3); also elsewhere on the board
/half bridges/ENA: U301.25 (PB12); also elsewhere on the board
/half bridges/IN1A: U301.32 (PA10); also elsewhere on the board
/half bridges/IN1B: U301.8 (PA0); also elsewhere on the board
/half bridges/IN2A: U301.31 (PA9); also elsewhere on the board
/half bridges/IN2B: U301.9 (PA1); also elsewhere on the board
/mcu/ADC1_IN12: R303.2, R304.1, U301.10 (PA2)
/mcu/CANH: U302.7 (CANH); also elsewhere on the board
/mcu/CANL: U302.6 (CANL); also elsewhere on the board
/mcu/CAN_RX: U301.47 (PB9), U302.4 (R)
/mcu/CAN_TX: U301.46 (PB8), U302.1 (D)
/mcu/DIR: U301.30 (PA8), U301.39 (PC10); also elsewhere on the board
/mcu/LED_FAULT: R302.1, U301.24 (PB11)
/mcu/LED_GOOD: R301.1, U301.22 (PB10)
/mcu/RESET: C308.1, J301.3 (~RESET), R306.2, U301.7 (PG10)
/mcu/STEP: U301.40 (PC11); also elsewhere on the board
/mcu/SWCLK: J301.4 (SWCLK), U301.37 (PA14)
/mcu/SWDIO: J301.2 (SWDIO), U301.36 (PA13)
/mcu/TIM4_CH1: J302.1, U301.44 (PB6)
/mcu/TIM4_CH2: J302.2, U301.45 (PB7)
/mcu/USBD_N: U301.33 (PA11); also elsewhere on the board
/mcu/USBD_P: U301.34 (PA12); also elsewhere on the board
/mcu/USER_1: J302.5, U301.29 (PC6)
/mcu/USER_2: J302.4, U301.28 (PB15)
/mcu/USER_3: J302.3, U301.27 (PB14), U301.38 (PA15)
/mcu/USER_BTN: R305.1, SW301.1, U301.4 (PC15)
/mcu/XIN: C305.1, U301.5 (PF0), Y301.1
/mcu/XOUT: C306.1, U301.6 (PF1), Y301.3
GND: C301.2, C302.2, C303.2, C304.2, C305.2, C306.2, C307.2, C308.2, D301.1 (K), D302.1 (K), J301.5 (GND), R304.2, R305.2, U301.49 (VSS), U302.2 (GND), U302.8 (Rs), Y301.2, Y301.4; also elsewhere on the board
unnamed: D301.2 (A), R301.2
unnamed: D302.2 (A), R302.2
unnamed: C301.1, C307.1, U301.20 (VREF+)
Vmot: R303.1; also elsewhere on the board

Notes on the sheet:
MT6835 ABI
I2C3_SDA, UART3_RX, STEP
I2C1_SDA
I2C1_SCL
MT6835 SPI
I2C3_SCL, DIR
UART3_TX, DIR

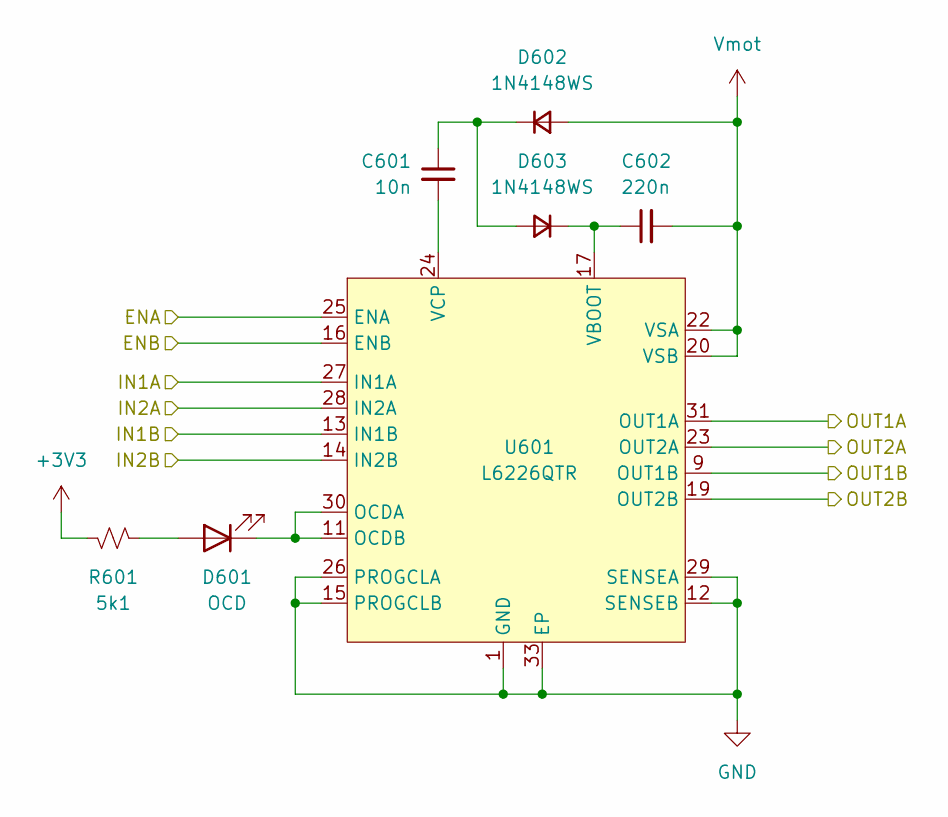
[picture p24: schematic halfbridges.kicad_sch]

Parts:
C601: 10n; C_0402_1005Metric; LCSC ID C15195
C602: 220n; C_0402_1005Metric; LCSC ID C16772
D601: OCD; D_0603_1608Metric; LCSC ID C2286
D602, D603: 1N4148WS; D_SOD-323; LCSC ID C2128
R601: 5k1; R_0402_1005Metric; LCSC ID C25905
U601: L6226QTR; ST-L6226Q-VQFN32; LCSC ID C95357

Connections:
+3V3: R601.2; also elsewhere on the board
/current sense/U_IN: U601.23 (OUT2A); also elsewhere on the board
/current sense/V_IN: U601.31 (OUT1A); also elsewhere on the board
/current sense/W_IN: U601.19 (OUT2B); also elsewhere on the board
/half bridges/ENA: U601.16 (ENB), U601.25 (ENA); also elsewhere on the board
/half bridges/IN1A: U601.27 (IN1A); also elsewhere on the board
/half bridges/IN1B: U601.13 (IN1B); also elsewhere on the board
/half bridges/IN2A: U601.28 (IN2A); also elsewhere on the board
/half bridges/IN2B: U601.14 (IN2B); also elsewhere on the board
/half bridges/OUT1B: U601.9 (OUT1B); also elsewhere on the board
GND: U601.1 (GND), U601.2 (NC), U601.3 (NC), U601.4 (NC), U601.5 (NC), U601.6 (NC), U601.7 (NC), U601.8 (NC), U601.12 (SENSEB), U601.15 (PROGCLB), U601.21 (GND), U601.26 (PROGCLA), U601.29 (SENSEA), U601.33 (EP); also elsewhere on the board
unnamed: D601.2 (A), R601.1
unnamed: D601.1 (K), U601.11 (OCDB), U601.30 (OCDA)
unnamed: C601.1, D602.1 (K), D603.2 (A)
unnamed: C602.1, D603.1 (K), U601.17 (VBOOT)
unnamed: C601.2, U601.24 (VCP)
Vmot: C602.2, D602.2 (A), U601.20 (VSB), U601.22 (VSA); also elsewhere on the board

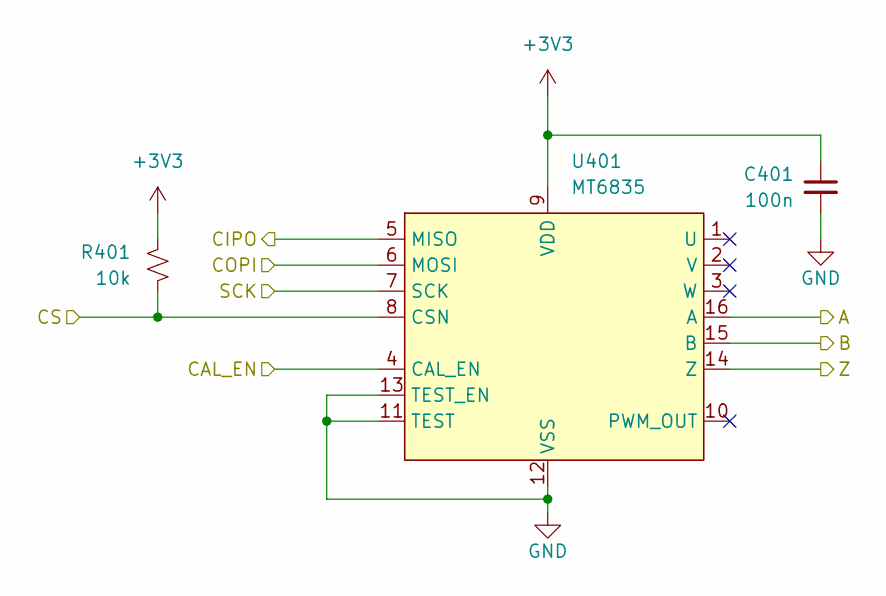
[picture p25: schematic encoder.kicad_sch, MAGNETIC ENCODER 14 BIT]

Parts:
C401: 100n; C_0402_1005Metric; LCSC ID C307331
R401: 10k; R_0402_1005Metric; LCSC ID C25744
U401: MT6835; TSSOP-16_4.4x5mm_P0.65mm; LCSC ID C2932578

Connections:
+3V3: C401.1, R401.1, U401.9 (VDD); also elsewhere on the board
/encoder/A: U401.16 (A); also elsewhere on the board
/encoder/B: U401.15 (B); also elsewhere on the board
/encoder/CAL_EN: U401.4 (CAL_EN); also elsewhere on the board
/encoder/CIPO: U401.5 (MISO); also elsewhere on the board
/encoder/COPI: U401.6 (MOSI); also elsewhere on the board
/encoder/CS: R401.2, U401.8 (CSN); also elsewhere on the board
/encoder/SCK: U401.7 (SCK); also elsewhere on the board
/encoder/Z: U401.14 (Z); also elsewhere on the board
GND: C401.2, U401.11 (TEST), U401.12 (VSS), U401.13 (TEST_EN); also elsewhere on the board

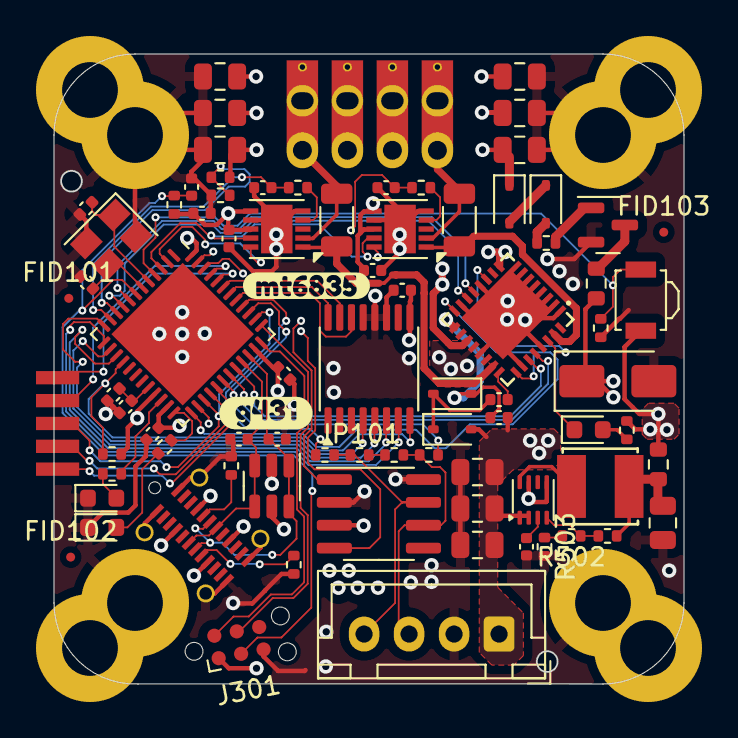
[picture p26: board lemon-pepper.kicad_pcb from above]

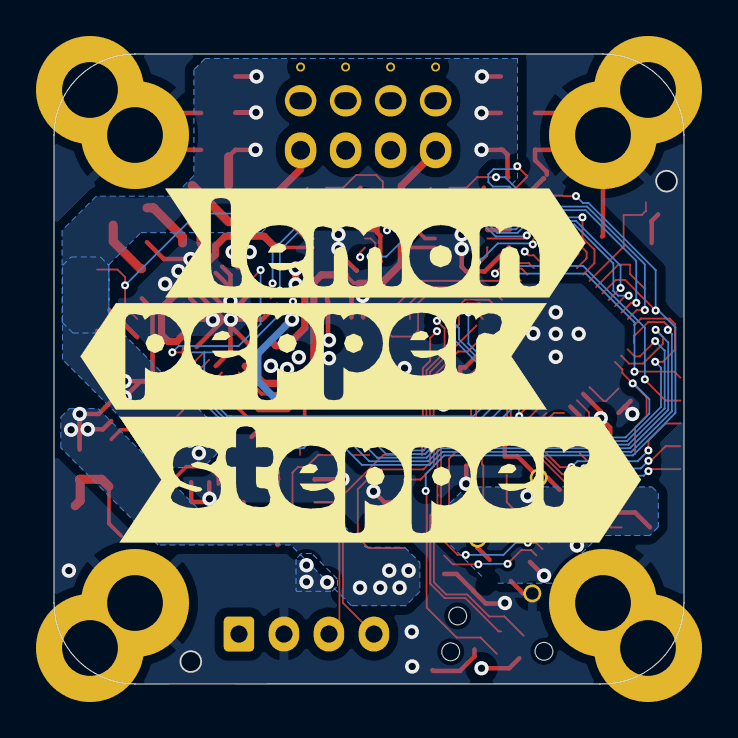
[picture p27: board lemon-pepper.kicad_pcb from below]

Board: 4 copper layers, 35.0 x 35.0 mm, 87 parts (3 on the bottom side), 71 nets.

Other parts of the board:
kibuzzard-652C57F7: G***; kibuzzard-652C57F7
kibuzzard-652C580D: G***; kibuzzard-652C580D
kibuzzard-694B0394: G***; kibuzzard-694B0394
kibuzzard-6557D15D: G***; kibuzzard-6557D15D
kibuzzard-6557D149: G***; kibuzzard-6557D149
kibuzzard-6557D153: G***; kibuzzard-6557D153

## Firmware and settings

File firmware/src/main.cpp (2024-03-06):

#include <Arduino.h>
#include <EEPROM.h>
#include <SPI.h>

#include <SimpleFOC.h>
#include "SimpleFOCDrivers.h"
#include "encoders/mt6835/MagneticSensorMT6835.h"
#include "encoders/stm32hwencoder/STM32HWEncoder.h"

#include "stm32g4xx_hal_conf.h"
#include "stm32g4xx_hal_fdcan.h"

#include "can.h"
#include "dfu.h"
#include "utils.h"
#include "InlineCurrentSenseSync.h"
#include "lemon-pepper.h"

#define USBD_MANUFACTURER_STRING "matei repair lab"
#define USBD_PRODUCT_STRING_FS "lemon-pepper-stepper"

// board specific data
typedef struct
{
	uint16_t signature;
	Direction electricalDir;
	float electricalZero;
	uint16_t abzResolution;
	uint8_t encoderCalibrated;
	uint8_t canID;
} userData;

userData boardData;
uint8_t updateData = 0;

const uint16_t magicWord = 0xAF0C;

// canbus things
extern volatile uint8_t TxData[8];
extern volatile uint8_t RxData[8];

// simpleFOC things
#define POLEPAIRS 50
#define RPHASE 3
#define MOTORKV 40
#define ENC_PPR 16383 // max 16383 (zero index) -> *4 for CPR, -1 is done in init to prevent rollover on 16 bit timer

#define SERIALPORT SerialUSB

// HardwareSerial Serial3 = HardwareSerial(PB8, PB9);

/**
 * SPI clockdiv of 16 gives ~10.5MHz clock. May still be stable with lower divisor.
 * The HW encoder is configured using PPR, which is then *4 for CPR (full 12384 gives overflow on 16 bit timer.)
 */
SPISettings myMT6835SPISettings(168000000 / 16, MT6835_BITORDER, SPI_MODE3);
MagneticSensorMT6835 sensor = MagneticSensorMT6835(ENC_CS, myMT6835SPISettings);
STM32HWEncoder enc = STM32HWEncoder(ENC_PPR, ENC_A, ENC_B, ENC_Z);

/**
 * TODO: Change the current sense code to reflect the new inline current sense amplifier choice with sense resistor.
 */
// InlineCurrentSenseSync currentsense = InlineCurrentSenseSync(90, ISENSE_U, ISENSE_V, ISENSE_W); // ACS711 current sensors
// InlineCurrentSenseSync currentsense = InlineCurrentSenseSync(0.02, 50, ISENSE_U, ISENSE_V, ISENSE_W); // max49925

StepperDriver4PWM driver = StepperDriver4PWM(MOT_A1, MOT_A2, MOT_B1, MOT_B2);
// StepperMotor motor = StepperMotor(POLEPAIRS, RPHASE, MOTORKV, 0.0045);
StepperMotor motor = StepperMotor(POLEPAIRS);
StepDirListener step_dir = StepDirListener(STEP_PIN, DIR_PIN, _2PI/200.0);
Commander commander = Commander(SERIALPORT);

uint16_t counter = 0;
float stepCounter;

DQCurrent_s foc_currents;
float electrical_angle;
PhaseCurrent_s phase_currents;

// Prototypes
uint8_t configureFOC(void);
uint8_t configureCAN(void);
uint8_t calibrateEncoder(void);

void userButton(void);
void onStep(void) {step_dir.handle();}

void setup()
{
	pinMode(LED_GOOD, OUTPUT);
	pinMode(LED_FAULT, OUTPUT);
	pinMode(CAL_EN, OUTPUT);
	pinMode(MOT_EN, OUTPUT);
	pinMode(USER_BUTTON, INPUT);
	pinMode(ISENSEGAIN_0, OUTPUT);
	pinMode(ISENSEGAIN_1, OUTPUT);

	attachInterrupt(USER_BUTTON, userButton, RISING);

	SerialUSB.begin();

	EEPROM.get(0, boardData);

	digitalWrite(MOT_EN, HIGH);
	digitalWrite(CAL_EN, LOW);

	digitalWrite(ISENSEGAIN_0, LOW);
	digitalWrite(ISENSEGAIN_1, HIGH);
	uint8_t ret;
	// ret = configureCAN();
	// if (!ret){
	// 	SIMPLEFOC_DEBUG("CAN init failed.");
	// 	digitalWrite(LED_FAULT, HIGH);
	// }

	ret = configureFOC();
	if (!ret){
		SIMPLEFOC_DEBUG("FOC init failed.");
		digitalWrite(LED_FAULT, HIGH);
	}

	if (sensor.getABZResolution() != ENC_PPR) // Check that PPR of the encoder matches our expectation.
	{
		digitalWrite(LED_FAULT, HIGH);
		SIMPLEFOC_DEBUG("Encoder ABZ resolution unexpected.");
	}

	// if (!boardData.encoderCalibrated) // If the encoder has not had self-calibration done, try.
	// {
	// 	uint8_t calibrationResult = calibrateEncoder();
	// 	if (calibrationResult == 0x3)
	// 	{
	// 		boardData.encoderCalibrated = 1;
	// 		updateData = 1;
	// 		SIMPLEFOC_DEBUG("Encoder self calibration successful.");
	// 	}
	// 	else
	// 	{
	// 		boardData.encoderCalibrated = 0;
	// 		digitalWrite(LED_FAULT, HIGH);
	// 		SIMPLEFOC_DEBUG("Encoder self calibration failed! Result: %#02x", calibrationResult);
	// 	}
	// }

	// if (boardData.canID == 0x000) // If the can ID is not set, then we'll look for a new, free ID.
	// {
	// 	uint8_t foundID = FDCAN_FindUniqueID();
	// 	if (foundID != 0)
	// 	{
	// 		boardData.canID = foundID;
	// 		updateData = 1;
	// 		SIMPLEFOC_DEBUG("Unique CAN ID found: %i", foundID);
	// 	} else {
	// 		digitalWrite(LED_FAULT, HIGH);
	// 		SIMPLEFOC_DEBUG("Failed to find a unique CAN ID!");
	// 	}
	// }

	// if(updateData) // If the configuration data has changed at all, update the flash.
	// {
	// 	EEPROM.put(0, boardData);
	// }
}

void loop()
{
	motor.loopFOC();
	motor.move();
	commander.run();

	if(counter == 0xFFF){
		digitalToggle(LED_GOOD);
		counter = 0;
	}

	counter++;

#ifdef HAS_MONITOR
	motor.monitor();
#endif
}

void doMotor(char *cmd)
{
	commander.motor(&motor, cmd);
}

uint8_t configureFOC(void)
{
	commander.add('M', doMotor, "motor");
	commander.verbose = VerboseMode::machine_readable;

#ifdef SIMPLEFOC_STM32_DEBUG
	SimpleFOCDebug::enable(&SERIALPORT);
#endif

	// Encoder initialization.
	// Ideally configuring the sensor over SPI then use STM32HWEncoder

	step_dir.init();
	step_dir.enableInterrupt(onStep);
	step_dir.attach(&stepCounter);

	enc.init();
	if (!enc.initialized)
		digitalWrite(LED_FAULT, HIGH);

	sensor.init();

	// Check if the encoder has loaded the right PPR, if not, update and then write to EEPROM.
	if (sensor.getABZResolution() != ENC_PPR)
	{
		delay(200);
		sensor.setABZResolution(ENC_PPR);
		sensor.writeEEPROM();

		digitalWrite(LED_GOOD, HIGH);
		digitalWrite(LED_FAULT, LOW);

		for (uint8_t i = 0; i < 60; i++)
		{ // Datasheet says we need to wait 6 seconds after writing EEPROM.
			digitalToggle(LED_GOOD);
			digitalToggle(LED_FAULT);
			delay(100);
		}

		digitalWrite(LED_GOOD, LOW);
		digitalWrite(LED_FAULT, LOW);
	}

	// Driver initialization.
	driver.pwm_frequency = 32000;
	driver.voltage_power_supply = 12;
	driver.voltage_limit = driver.voltage_power_supply / 2;
	driver.init();

	// Motor PID parameters.
    motor.PID_velocity.P = 0.035;
    motor.PID_velocity.I = 0.01;
    motor.PID_velocity.D = 0.000;
    motor.LPF_velocity.Tf = 0.004;
	motor.PID_velocity.output_ramp = 750;
	motor.PID_velocity.limit = 500;

	motor.P_angle.P = 350;
    motor.P_angle.I = 8;
    motor.P_angle.D = 0.3;
    motor.LPF_angle = 0.001;
	motor.LPF_angle.Tf = 0; // try to avoid

	// Motor initialization.
	// motor.voltage_sensor_align = 2;
	motor.current_limit = 1;
	motor.velocity_limit = 500;
	motor.controller = MotionControlType::velocity;
	motor.foc_modulation = FOCModulationType::SpaceVectorPWM;

// Monitor initialization
#ifdef HAS_MONITOR
	motor.useMonitoring(SERIALPORT);
	motor.monitor_start_char = 'M';
	motor.monitor_end_char = 'M';
	motor.monitor_downsample = 250;
#endif

	motor.linkSensor(&sensor);
	motor.linkDriver(&driver);

	// currentsense.linkDriver(&driver);
	// int ret = currentsense.init();
	// SERIALPORT.printf("Current Sense init result: %i\n", ret);
	// motor.linkCurrentSense(&currentsense);

	sensor.update();
	float start_angle = motor.shaftAngle();
	motor.target = start_angle;
	SIMPLEFOC_DEBUG("Setting Motor target to current position");

	motor.zero_electric_angle = NOT_SET;
	motor.sensor_direction = Direction::UNKNOWN;

	motor.init();
	motor.initFOC();

	// if(boardData.signature != magicWord){
	// 	// If we have not initialized the EEPROM before.
	// 	motor.init();
	// 	motor.initFOC();

	// 	boardData.signature = magicWord;
	// 	boardData.electricalZero = motor.zero_electric_angle;
	// 	boardData.electricalDir = motor.sensor_direction;
	//  updateData = 1;
	// }
	// else{
	// 	motor.zero_electric_angle = boardData.electricalZero;
	// 	motor.sensor_direction = boardData.electricalDir;
	// 	motor.init();
	// 	motor.initFOC();
	// }

	return 1;
}

uint8_t configureCAN(void)
{
	FDCAN_Start(0x000);
	return 1;
}

uint8_t calibrateEncoder(void)
{
	motor.target = 35; // roughly 2000rpm -> need to write 0x1 to Reg. AUTOCAL_FREQ

	MT6835Options4 currentSettings = sensor.getOptions4();
	currentSettings.autocal_freq = 0x1;
	sensor.setOptions4(currentSettings);

	uint32_t calTime = micros();
	while ((micros() - calTime) < 2000000)
	{
		motor.loopFOC();
		motor.move();

		if ((micros() -calTime) > 2000)
		{
			// after motor is spinning at constant speed, enable calibration.
			digitalWrite(LED_GOOD, HIGH);
			digitalWrite(CAL_EN, HIGH);
		}
	}

	digitalWrite(LED_GOOD, LOW);
	digitalWrite(CAL_EN, LOW);

	return sensor.getCalibrationStatus();
}

void userButton(void)
{
	if(USB->DADDR != 0)
		jump_to_bootloader();
	else
		digitalToggle(LED_FAULT);
}

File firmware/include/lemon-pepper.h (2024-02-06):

#pragma once

#ifdef LEMONPEPPER

// MOTOR DRIVER L6226
#define U_PWM       PA10    // TIM2_CH4
#define V_PWM       PA9     // TIM2_CH3
#define W_PWM       PA1     // TIM2_CH2

#define MOT_A1      PA0     // TIM2_CH1
#define MOT_A2      PA10    // TIM2_CH4
#define MOT_B1      PA9     // TIM2_CH3
#define MOT_B2      PA1     // TIM2_CH2

#define MOT_EN      PB12

// ENCODER MT6835
#define ENC_A       PB4     // TIM3_CH1
#define ENC_B       PB5     // TIM3_CH2
#define ENC_Z       PB3     // TIM3_ETR

#define ENC_COPI    PA7     // SPI1_MOSI
#define ENC_CIPO    PA6     // SPI1_MISO
#define ENC_SCK     PA5     // SPI1_SCK
#define ENC_CS      PC4     

#define CAL_EN      PA4

// CURRENT SENSE
#define ISENSE_U    PA3     // VOPAMP1_P, ADC1_IN4
#define ISENSE_V    PB13    // VOPAMP3_P

/**
 * 0b00 10V/V
 * 0b01 20V/V
 * 0b10 50V/V
 * 0b11 100V/V
*/
#define ISENSEGAIN_0 PC13   // GAIN0 
#define ISENSEGAIN_1 PC14   // GAIN1

// COMMUNICATION
/** 
 * Note that you can only use one input peripheral 
 * at a time. If  you want to use CANbus you also have 
 * to remove the resistors that join step-dir to CAN H/L
 * R104 R105 to protect MCU from high common mode voltages.
*/
#define CAN_TX      PB8
#define CAN_RX      PB9

#define UART3_TX    PC10
#define UART3_RX    PC11

#define I2C3_SDA    PC11
#define I2C3_SCL    PA8

#define STEP_PIN    PC10
#define DIR_PIN     PC11

// USER CONNECTOR
/**
 * Additional timer available for encoder interface. 
 * If not using, there are 5 GPIO available.
*/
#define USER_ENCA   PB6     // TIM4_CH1
#define USER_ENCB   PB7     // TIM4_CH2

#define USER1       PC6
#define USER2       PB15
#define USER3       PB14
#define USER4       PB7
#define USER5       PB6

// MISC
#define USER_BUTTON PC15
#define LED_GOOD    PB10
#define LED_FAULT   PB11
#define MOT_VOLTAGE PA2     //ADC1_IN3

#endif

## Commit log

2023-10-12 finish component selection
    [currentsense.kicad_sch, driver.kicad_sch, encoder.kicad_sch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]
2023-10-12 reverse polarity diode
    [lemon-pepper.kicad_sch]
2023-10-17 try new driver
    [currentsense.kicad_sch, driver.kicad_sch, fets.kicad_sch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]
2023-10-18 change driver configuration
    [currentsense.kicad_sch, lemon-pepper.kicad_pcb, lemon-pepper.kicad_sch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]
2023-10-18 finish layout and prod files
    [currentsense.kicad_sch, halfbridges.kicad_sch, lemon-pepper-BOM.csv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]
2023-10-18 board logo
    [lemon-pepper-B_Cu.gbr, lemon-pepper-B_Mask.gbr, lemon-pepper-B_Paste.gbr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]
2023-10-19 update fab files
    [lemon-pepper-B_Cu.gbr, lemon-pepper-B_Mask.gbr, lemon-pepper-B_Paste.gbr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]
2023-10-19 fix fab files (again)
    [lemon-pepper-B_Cu.gbr, lemon-pepper-B_Mask.gbr, lemon-pepper-B_Paste.gbr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]
2023-10-20 rework power plane
    [currentsense.kicad_sch, encoder.kicad_sch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]
2023-10-20 add readme and update fab files
    [currentsense.kicad_sch, usb.kicad_sch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]
2023-10-20 tweak pours
    [lemon-pepper-B_Cu.gbr, lemon-pepper-B_Mask.gbr, lemon-pepper-B_Paste.gbr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]
2023-10-22 work on analog layout
    [currentsense.kicad_sch, encoder.kicad_sch, lemon-pepper-BOM.csv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]
2023-10-22 finallize rev 1 layout
    [lemon-pepper-B_Cu.gbr, lemon-pepper-B_Mask.gbr, lemon-pepper-B_Paste.gbr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]
2023-10-22 firmware defines
    [currentsense.kicad_sch, lemon-pepper.kicad_pcb, mcu.kicad_sch]
2023-10-22 fix current sense pn
    [currentsense.kicad_sch, lemon-pepper-BOM.csv]
2023-10-22 shift B1 trace slightly
    [lemon-pepper-BOM.csv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]
2023-10-23 clean up ERC in schematic
    [currentsense.kicad_sch, encoder.kicad_sch, halfbridges.kicad_sch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]
2023-10-23 change vias to 0.2/0.45mm for cheaper production
    [lemon-pepper-B_Cu.gbr, lemon-pepper-B_Mask.gbr, lemon-pepper-B_Paste.gbr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]
2023-10-23 roll nema14 and nema17 into same branch
    [currentsense.kicad_sch, lemon-pepper-BOM.csv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]
2023-10-24 change pins to support I2C input
    [currentsense.kicad_sch, lemon-pepper.kicad_pcb, mcu.kicad_sch]
2023-10-26 fix via sizing
    [lemon-pepper-B_Cu.gbr, lemon-pepper-B_Mask.gbr, lemon-pepper-B_Paste.gbr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]
2023-10-28 update firmware defines to support pcb rev 2
2023-11-02 fix bringup issues
    [currentsense.kicad_sch, encoder.kicad_sch, lemon-pepper.kicad_pcb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]
2023-11-02 remove stray files/folders
    [lemon-pepper.kicad_pcb]
2023-11-06 start working on current sense
    [currentsense.kicad_sch, lemon-pepper.kicad_pcb, mcu.kicad_sch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]
2023-11-08 bringup changes
    [currentsense.kicad_sch, lemon-pepper-BOM.csv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]
2023-11-09 redraw USB C connector with proper mounting holes
    [currentsense.kicad_sch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]
2023-11-09 work on current sense
    [currentsense.kicad_sch, lemon-pepper.kicad_pcb, mcu.kicad_sch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]
2023-11-11 Change references to BLDCDriver to FOCDriver in current sense base class
    change setPwm function in FOCDriver to accept 3 args, with a default value for the 3rd
    Change stepper driver classes to use 3 arg setPwm, ignoring 3rd arg.
    created InlineCurrentSenseSync class in lib/currentsense.
    fixed timer bug in calibrate encoder, in main
    defined a label for serialusb, to make it easier to swap out.
    [main.cpp]
2023-11-11 Add some debug prints
    fix function def for init ADC, so it overrides the weak generic version
    fix caps in mt6835 include so gcc is happy
    [main.cpp]
2023-11-11 add idea for heatsink NEMA14
    [heatsink-nema-14.step, heatsink-nema-14.stl, heatsink.FCStd]
2023-11-11 update pcb layout
    [currentsense.kicad_sch, lemon-pepper.kicad_pcb, lemon-pepper.kicad_sch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]
2023-11-12 current sense LPF prototype
    [currentsense.kicad_sch, lemon-pepper.kicad_pcb]
2023-11-12 heatink prototype
    [heatsink-nema-14.step, heatsink-nema-14.stl, heatsink.FCStd]
2023-11-12 get ADC trigger working
2023-11-13 improve DFM
    [heatsink-nema-14.step, heatsink-nema-14.stl, heatsink.FCStd]
2023-11-14 add user button
    [currentsense.kicad_sch, lemon-pepper.kicad_pcb, lemon-pepper.kicad_sch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]
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2023-11-14 fix thermal contact placement
    [heatsink-nema-14.step, heatsink-nema-14.stl, heatsink.FCStd]
2023-11-15 got current sense readings!
2023-11-15 add vmotor pin in gpio init
2023-11-15 fix opamp instance fix voltage scale in utils.cpp fix switch case for pins in _readADCVoltageInline
    added commented out lines for my motor config, changed PID values, added global monitor variables near loop
    [main.cpp]
2023-11-17 finalize v3 files
    [currentsense.kicad_sch, lemon-pepper-BOM.csv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]
2023-11-17 update step file
    [heatsink.FCStd]
2023-11-18 rev3 documentation
    [currentsense.kicad_sch, lemon-pepper.kicad_sch, mcu.kicad_sch]
2023-11-18 add DFU button. update defines for v3
2023-12-10 change inductor footprint, add I2C1 SCL on user 3
    [currentsense.kicad_sch, lemon-pepper.kicad_pcb, mcu.kicad_sch]
2023-12-10 update documentation
    [mcu.kicad_sch]
2023-12-18 update L6226Q footprint and symbol
    [halfbridges.kicad_sch, lemon-pepper.kicad_pcb]
2024-01-13 v3 fixes, appropriate inductor
    [lemon-pepper-BOM.csv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]
2024-01-13 Changed initial motor setpoint to the current angle, so that motor doesn't make a violent move on startup
    [main.cpp]
2024-01-23 Made analog gain of current sense amps selectable by mcu. Removed analog ground plane and tied all grounds together
    [currentsense.kicad_sch, halfbridges.kicad_sch, lemon-pepper.kicad_pcb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]
2024-01-30 get DRC clean
    [lemon-pepper-B_Cu.gbr, lemon-pepper-B_Mask.gbr, lemon-pepper-B_Paste.gbr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]
2024-01-30 add tooling holes, update CPL
    [lemon-pepper-B_Cu.gbr, lemon-pepper-B_Mask.gbr, lemon-pepper-B_Paste.gbr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]
2024-02-06 Update firmware defines to match hardware
    [encoder.kicad_sch, halfbridges.kicad_sch, lemon-pepper.kicad_sch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]
2024-02-28 fix erc failures
    [currentsense.kicad_sch, encoder.kicad_sch, halfbridges.kicad_sch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]
2024-03-01 Push schematics to repo via gha
2024-03-05 fix current sense pinout
    [currentsense.kicad_sch, lemon-pepper.kicad_pcb]
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2024-03-05 Remove assembly folder as now documentation comes from artifact
    [lemon-pepper-BOM.csv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]
2024-03-05 Update BOM field LCSC ID
    [currentsense.kicad_sch, encoder.kicad_sch, halfbridges.kicad_sch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]
2024-03-06 add firmware control of current sense gain pins add commented call to initialize current sense object
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2024-06-24 add mechanical models
    [NEMA_14_motor.step, stepper-models.FCStd, usb_c.FCStd]
2025-11-10 update to kicad 9
    [currentsense.kicad_sch, encoder.kicad_sch, halfbridges.kicad_sch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]
2025-11-10 fix BOM to use basic parts again
    [mcu.kicad_sch, psu.kicad_sch, usb.kicad_sch]
2025-11-18 bump trace width in key areas
    [lemon-pepper.kicad_pcb]
2025-11-18 fix inductor input trace
    [lemon-pepper.kicad_pcb]
2025-12-23 add hybrid board outline
    [lemon-pepper.kicad_pcb, lemon-pepper.kicad_sch, psu.kicad_sch]
2025-12-23 clean erc drc, pack sym, footprints into standalone lib
    [currentsense.kicad_sch, encoder.kicad_sch, halfbridges.kicad_sch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]
2025-12-24 add step model for new heatsink
    [heatsink-nema-14-17.step, heatsink-nema-14.step, heatsink-nema-14.stl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]
